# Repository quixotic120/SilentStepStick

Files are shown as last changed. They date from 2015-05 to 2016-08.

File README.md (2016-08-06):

# fork of SilentStepStick
The Silent-Step-Stick is a Stepper Motor Driver Board based on a [Trinamic TMC 2100](http://www.trinamic.com/products/integrated-circuits/stepper-power-driver/tmc2100) or [Trinamic TMC 2130](http://www.trinamic.com/products/integrated-circuits/stepper-power-driver/tmc2130).
The driver boards are hardware compatible with [StepStick](http://reprap.org/wiki/StepStick) and [Pololu A4988](https://www.pololu.com/product/1182).

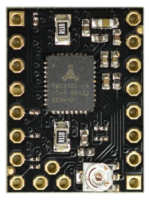
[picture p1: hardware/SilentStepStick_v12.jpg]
SilentStepStick TMC2100 (3.3-5V) (http://www.watterott.com/en/SilentStepStick)

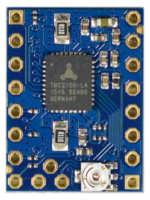
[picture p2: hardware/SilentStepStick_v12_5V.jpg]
SilentStepStick TMC2100 (5V) (http://www.watterott.com/en/SilentStepStick-TMC2100-5V)

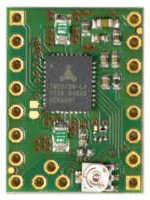
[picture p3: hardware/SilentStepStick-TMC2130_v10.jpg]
SilentStepStick TMC2130 (3.3-5V) (http://www.watterott.com/en/SilentStepStick-TMC2130)

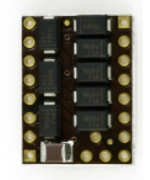
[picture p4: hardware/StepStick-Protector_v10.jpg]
SilentStepStick Protector (http://www.watterott.com/en/SilentStepStick-Protector)


## Shop
* Trinamic **TMC2100** based drivers (CFG pins for configuration)
  * [TMC2100 SilentStepStick (3.3-5V logic voltage)](http://www.watterott.com/en/SilentStepStick)
  * [TMC2100 SilentStepStick (3.3-5V logic voltage) with soldered Pin Headers](http://www.watterott.com/en/SilentStepStick-with-Pins)
  * [TMC2100 SilentStepStick (5V logic voltage)](http://www.watterott.com/en/SilentStepStick-TMC2100-5V)
  * [TMC2100 SilentStepStick (5V logic voltage) with soldered Pin Headers](http://www.watterott.com/en/SilentStepStick-TMC2100-5V-with-Pins)
* Trinamic **TMC2130** based drivers (SPI for configuration)
  * [TMC2130 SilentStepStick (3.3-5V logic voltage)](http://www.watterott.com/en/SilentStepStick-TMC2130)
* Accessories
  * [SilentStepStick Protector (with flyback diodes)](http://www.watterott.com/en/SilentStepStick-Protector)
  * [Suitable Heatsink 10x10mm](http://www.watterott.com/en/Pin-heatsink-square-ICK-S-10-x-10-x-125)
  * [Suitable Heatsink 10x6mm](http://www.watterott.com/en/Heatsink-for-DIL-IC-PLCC-und-SMD-10-x-6-mm)
  * [Suitable Heatsink 8x6mm](http://www.watterott.com/en/Heatsinks-6-3x8mm)

## Features
* Hardware compatible with [StepStick](http://reprap.org/wiki/StepStick) and [Pololu A4988](https://www.pololu.com/product/1182)
* Trinamic TMC21x0 stepper motor driver
* Step/Dir interface with up to 16 microsteps and 256 microsteps interpolation
* Motor current: up to **1.2A RMS** continuously and 2.5A short time peak current per coil
* Motor voltage: **5.5...45V** (3.3...5V logic) or **4.75...45V** (5V logic)
* **microPlyer** - microstep interpolator for increased smoothness of microstepping
* **stealthChop** - for quiet operation and smooth motion
* **spreadCycle** - highly dynamic motor control chopper
* Extra features of **TMC2130**:
  * SPI configuration interface (up to 4MHz)
  * up to 256 native microsteps (without interpolation)
  * **coolStep** - current control for energy savings
  * **stallGuard** - sensorless motor load detection
  * **dcStep** - load dependent speed control

## Hardware
* [Schematics/Layout + Guide](https://github.com/watterott/SilentStepStick/tree/master/hardware)
* [FAQ (Frequently Asked Questions)](https://github.com/watterott/SilentStepStick/blob/master/docu/FAQ.md)
* [Eagle CAD Part](https://github.com/watterott/Eagle-Libs)

## Reviews and Tests

* Review from Thomas Sanladerer:

  SilentStepStick/TMC2100 Review (https://www.youtube.com/watch?v=g6Bxoqr8QlY)

  SilentStepStick/TMC2100 Review Update (https://www.youtube.com/watch?v=mYuZqx8xwTg)

* Review from Peter Recktenwald:

  SilentStepStick/TMC2100 Review (https://www.youtube.com/watch?v=P3ebhi-vZRY)

* Review from Georg Mill:

  [](http://blog.georgmill.de/2015/06/18/schrittmotor-test-5-treiber-im-vergleich/)

* What is Trinamic stallGuard2 and coolStep:

  Trinamic stallGuard2 and coolStep (https://www.youtube.com/watch?v=Prw7wNa20Gk)

* Tests:
  * [Watterott (Stepper Motor)](https://www.youtube.com/watch?v=0l-HlntFYOY)
  * [Aleks (RepRap Prusa i3)](https://www.youtube.com/watch?v=33jQ0P7SMJA)
  * [Anthony (Delta Printer)](https://www.youtube.com/watch?v=CZOV0BdgSiU)
  * [Mario Lukas](https://www.youtube.com/watch?v=mJmg0iRHX8s)
  * Yusuke Sasaki: [TMC2100 steahlChop](https://www.youtube.com/watch?v=wrS7l46YJ_E), [TMC2100 spreadCycle](https://www.youtube.com/watch?v=391TY72wzPQ), [A4988](https://www.youtube.com/watch?v=iw6MRjzS6V4)
  * [MakerSpatz (Ultimaker)](https://www.youtube.com/watch?v=0jPbzB7XtWg)
  * [Aitor Esteve Alvarado (Ninja Prusa i3)](https://www.youtube.com/watch?v=c_TCVirnKJ0)
  * [Artur Wronowski (Delta Printer)](https://www.youtube.com/watch?v=hH2UkAmbfYs)
  * [3D Huynh (Felix 3D)](https://www.youtube.com/watch?v=EglFOpTXPtg)
  * [Easy 3D (Sparkcube)](https://www.youtube.com/watch?v=BxE_F8_Ec8M)
  * [WOLF HSW (linear drive)](https://www.youtube.com/watch?v=wjuAu0WYOPM)
  * Clarence Lee (ATOM Delta Printer): [TMC2100](https://www.youtube.com/watch?v=sBVNqFybUZI), [DRV8825](https://www.youtube.com/watch?v=tNufJnybsxg), [A4982](https://www.youtube.com/watch?v=r1noUt2UoO8)
  * Alex Tien (3DP Delta Printer): [TMC2100](https://www.youtube.com/watch?v=RcqnXXp4tPA), [A4988](https://www.youtube.com/watch?v=F2oB_NOLxHU)
  * swdjojo (Prusa i3): [TMC2100](https://www.youtube.com/watch?v=vBRNifmHaZE), [A4988](https://www.youtube.com/watch?v=TCgErVx93OA)
  * [Doc. Snuggles (Stepper Motor)](https://www.youtube.com/watch?v=gj6f6HSrHc4)
  * [Robert Sertic (Ultimaker)](https://www.youtube.com/watch?v=1wQJZb0gzoE)
  * [Emanuel Kant (Ultimaker)](https://www.youtube.com/watch?v=Y7CG43yf9zA)
  * [ghicione (EggBot)](https://www.youtube.com/watch?v=4FBAAQXnESU)
  * Edward Kuo: [E3D Cyclops Delta Printer](https://www.youtube.com/watch?v=iEYdrMH69oo), [TMC2100 water cooled](https://www.youtube.com/watch?v=vjNM9R0NZG0)
  * [Noah Ahmad Connor (Prusa i3)](https://www.youtube.com/watch?v=mNdl3s8TYmY)
  * [Sterillium (XYZ DaVinci)](https://www.youtube.com/watch?v=k-szP5wuplM)
  * [markg21405 (Delta Printer)](https://www.youtube.com/watch?v=tytL3KeIlLw)
  * [JJiG (MakerFarm Pegasus)](https://www.youtube.com/watch?v=9Rny6n1MCfI)
  * [René Jurack (Skimmy v3)](https://www.youtube.com/watch?v=qpl8v0k1_34)
  * [David Spaulding (A4988 vs. TMC2100)](https://www.youtube.com/watch?v=Z5OQpMSvWvs)
  * [Tarjeik (DRV8825 vs. TMC2100)](https://www.youtube.com/watch?v=oNAHOOolHWw)

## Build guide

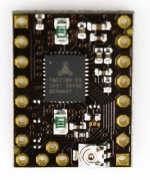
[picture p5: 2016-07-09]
hardware/SilentStepStick_v11.jpg

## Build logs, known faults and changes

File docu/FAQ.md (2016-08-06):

# Frequently Asked Questions

## Is the SilentStepStick 100% compatible with a StepStick or Pololu A4988?
The SilentStepStick is hardware/pin compatible with StepStick and Pololu A4988 drivers.
However the TMC2100 has different and more settings, which can be set via the CFG/MS pins.
The TMC2100 config pins also know three states: low (GND), high (VIO) and open (unconnected).
On the TMC2130 SPI is used for the configuration and so the controller board must have SPI on the CFG pins.

## Where can I find more information on the settings and operation modes?
More information can be found in the [SilentStepStick schematics](https://github.com/watterott/SilentStepStick/tree/master/hardware) and [TMC2100 datasheet](http://www.trinamic.com/products/integrated-circuits/stepper-power-driver/tmc2100) / [TMC2130 datasheet](http://www.trinamic.com/products/integrated-circuits/stepper-power-driver/tmc2130).
For most cases the **1/16 stealthChop** mode (CFG1=open, CFG2=open, CFG3=open) is suitable.
If you have problems like step losses then use the more powerful **1/16 spreadCycle** mode (CFG1=GND, CFG2=open, CFG3=open).

#### Installation Guides for 3D Printers
* [General (English)](http://reprap.org/wiki/TMC2100)
* [General (German)](http://reprap.org/wiki/TMC2100/de)
* [General (Russian)](http://3deshnik.ru/blogs/akdzg/chto-zhe-delat-belami-tmc2100)
* [General (Japanese)](http://3dp0.com/silentstepstick)
* [RAMPS (English)](http://www.instructables.com/id/Install-and-configure-SilentStepStick-in-RAMPS-TMC/)
* [Ultimaker UMO + TMC2100 (English)](https://ultimaker.com/en/community/11571-step-by-step-installation-of-silentstepstick-drivers-on-umo)
* [Ultimaker UMO + TMC2130 (English)](https://ultimaker.com/en/community/20090-step-by-step-installation-of-sss-tmc2130-on-umo)

#### Boards with USB Power Supply and SilentStepSticks with 3.3...5V logic voltage
If you use a control board with USB power supply (like Arduino + RAMPS) then always ensure that ```VM``` is present, when you connect the board via USB.
Otherwise the TMC21x0 is not powered via the internal voltage regulator and a high current can flow into ```VIO``` and this can damage the internal logic.
As safety workaround you can disconnect the 5V signal in the USB cable, so that the board cannot be powered over USB.

#### RAMPS 1.4 and RUMBA Notes
If you remove all jumpers (or open all switches) for MS1+MS2+MS3, then the SilentStepStick TMC2100 driver will be in 1/16 spreadCycle mode (CFG1=GND, CFG2=open, CFG3=open), because there is a pull-down resistor on MS1 on the RAMPS.
But if you have not an original [RAMPS 1.4](http://reprap.org/wiki/RAMPS_1.4) or [RUMBA](http://reprap.org/wiki/RUMBA), then your schematics can be different and you have to check the MS-Pin configurations on you board.

## How to set the stepper motor current?
The best way to set the motor current is by measuring the voltage on the ```Vref``` pin (0...2.5V) and
adjusting the voltage with the potentiometer.
The maximum motor current is 1.77A RMS and is set via the 0.11Ohm sense resistors.

```Irms = (Vref * 1.77A) / 2.5V = Vref * 0.71```

```Vref = (Irms * 2.5V) / 1.77A = Irms * 1.41```

**Example:** A voltage of 1.0V on Vref sets the motor current to 0.71A RMS.

**Note:** On some stepper motor drivers the maximum current (e.g. A4988) is set via Vref and on others the RMS current (e.g. TMC2100).
          ```Imax = 1.41 * Irms```

## What to consider when turning the power supply on or off?
**Power on:**
The motor supply voltage ```VM``` should come up first and then ```VIO```, because the internal logic of the TMC21x0 driver is powered from ```VM``` (SilentStepSticks with 3.3...5V logic voltage).
Only after ```VIO``` is present and stable, the driver inputs (STEP, DIR, EN, CFG1...) can be driven with a high level.

Because ```VM``` is a strong power supply with a high voltage, also ensure that there cannot occur voltage spikes on power up. See [Pololu: Understanding Destructive LC Voltage Spikes](https://www.pololu.com/docs/0J16/all).

**Power off:**
If the motor is running/moving, then it is not allowed to switch off the power supply. Always make sure that the motor stands still on shutting down otherwise the TMC21x0 driver can get damaged.
An **emergency stop** can be realized, when the ```EN/CFG6``` pin is set to ```VIO```. This will switch off all power drivers and will put the motor into freewheeling.
See also: [SilentStepStick Protector with flyback diodes](https://github.com/watterott/SilentStepStick#shop)

## The motor makes noise in spreadCycle mode when it is not moving?
A motor supply voltage of 12V is in most cases to low and in general the sound gets quieter if the motor supply voltage is above 18V.

## How to control the TMC21x0 stepper motor driver?
The SilentStepStick has a normal step+direction interface.
You set the direction with the ```DIR``` pin and on every pulse on the ```STEP``` pin the motor will move one step.
Here you can find an [Arduino example](https://github.com/watterott/SilentStepStick/tree/master/software) and [Arduino library](http://www.airspayce.com/mikem/arduino/AccelStepper/) (interface=DRIVER).

## Is it possible to connect the CFG pins from different SilentStepSticks?
It is possible to connect the ```CFG``` pins from two or more driver boards.
However then the pin state can only be ```GND``` (low) or ```VIO``` (high). The open state (unconnected) is not possible in this configuration.

## Why is the TMC2100 chip on the bottom PCB side?
The TMC2100/TMC2130 chip has a thermal pad on the bottom which is soldered to the PCB.
So the thermal resistance via the chip bottom is better than via the top.
That is why the chip is on the bottom PCB side.
A heat sink can be placed directly on the PCB.
Further infos [here](https://www.youtube.com/watch?time_continue=145&v=mYuZqx8xwTg).

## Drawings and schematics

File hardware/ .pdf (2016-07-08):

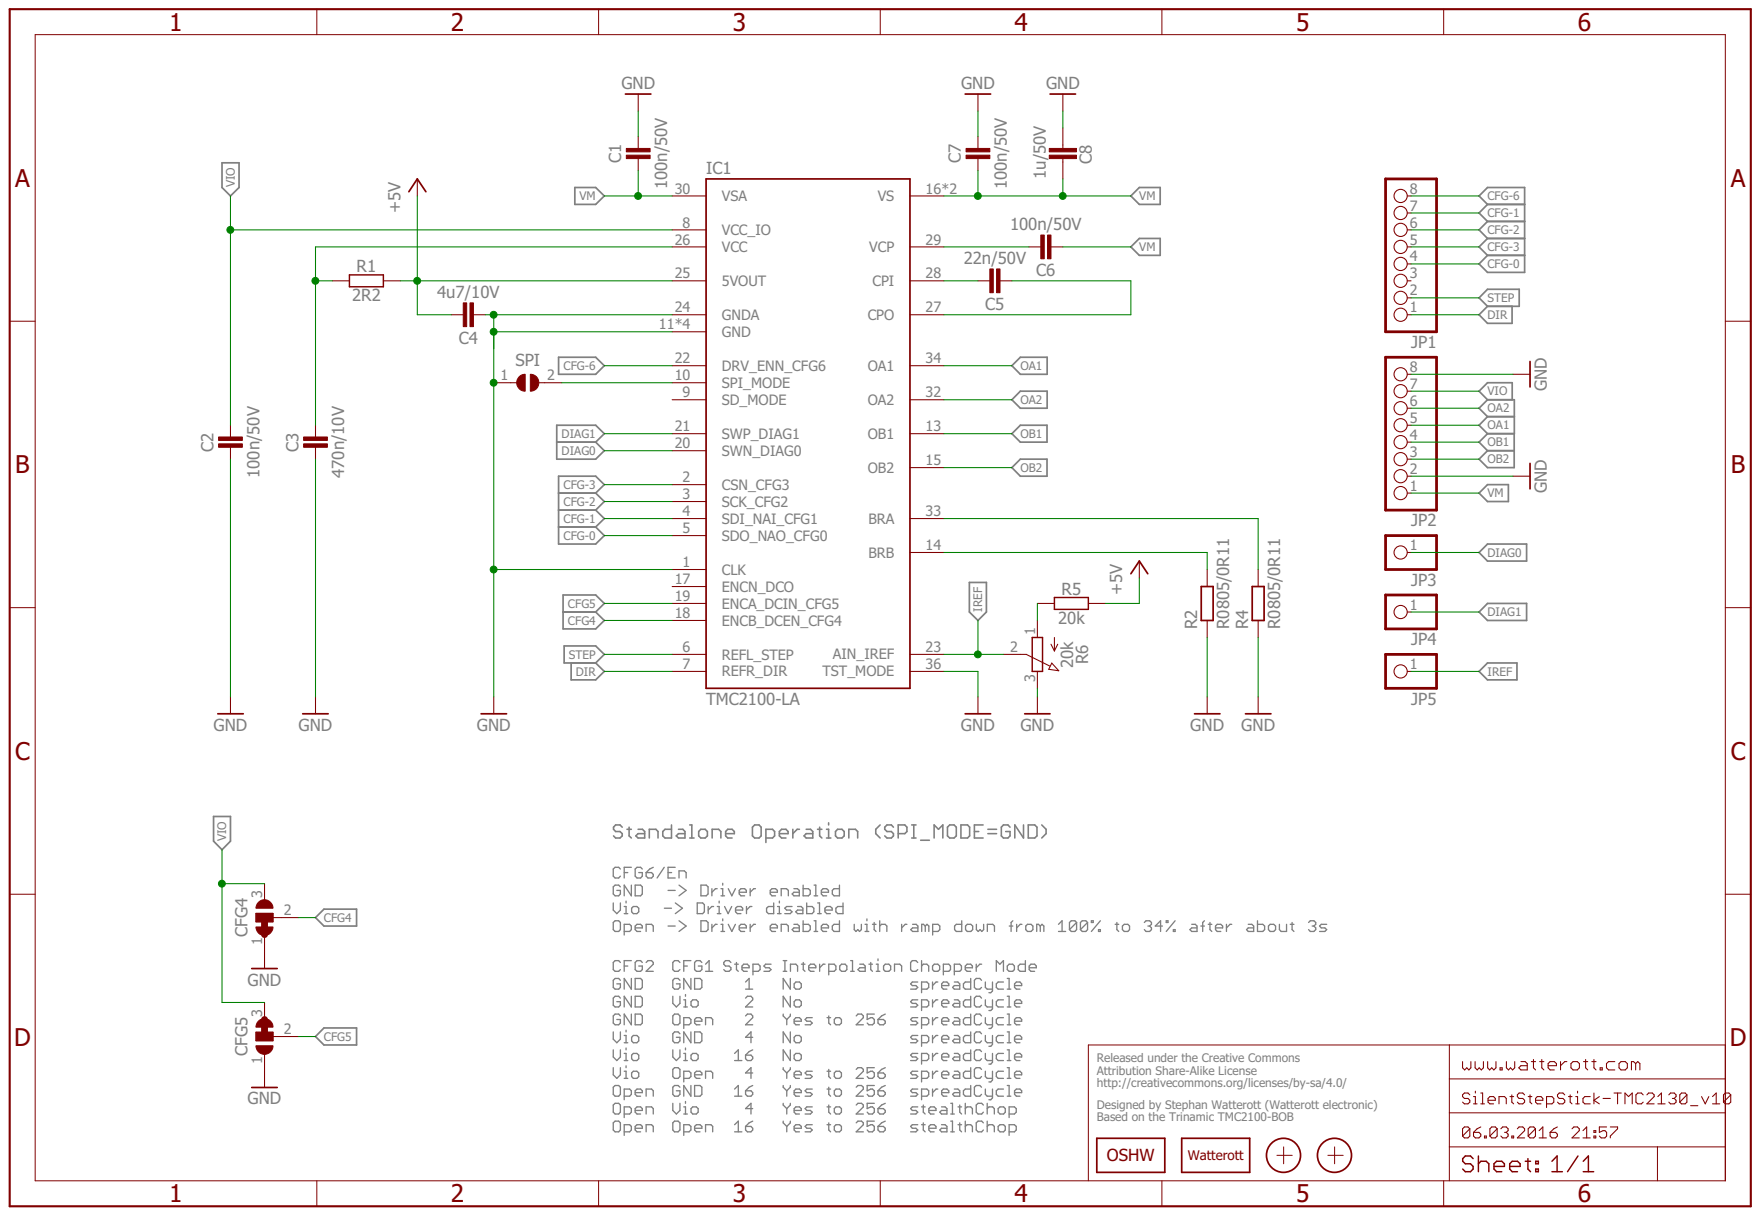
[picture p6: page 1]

VCC 26

R1 | 5VOUT 25

GNDA 24

Released under the Creative Commons
Attribution Share-Alike License
http://creativecommons.org/licenses/by-sa/4.0/

Designed by Stephan Watterott (Watterott electronic)
Based on the Trinamic TMC2100-BOB

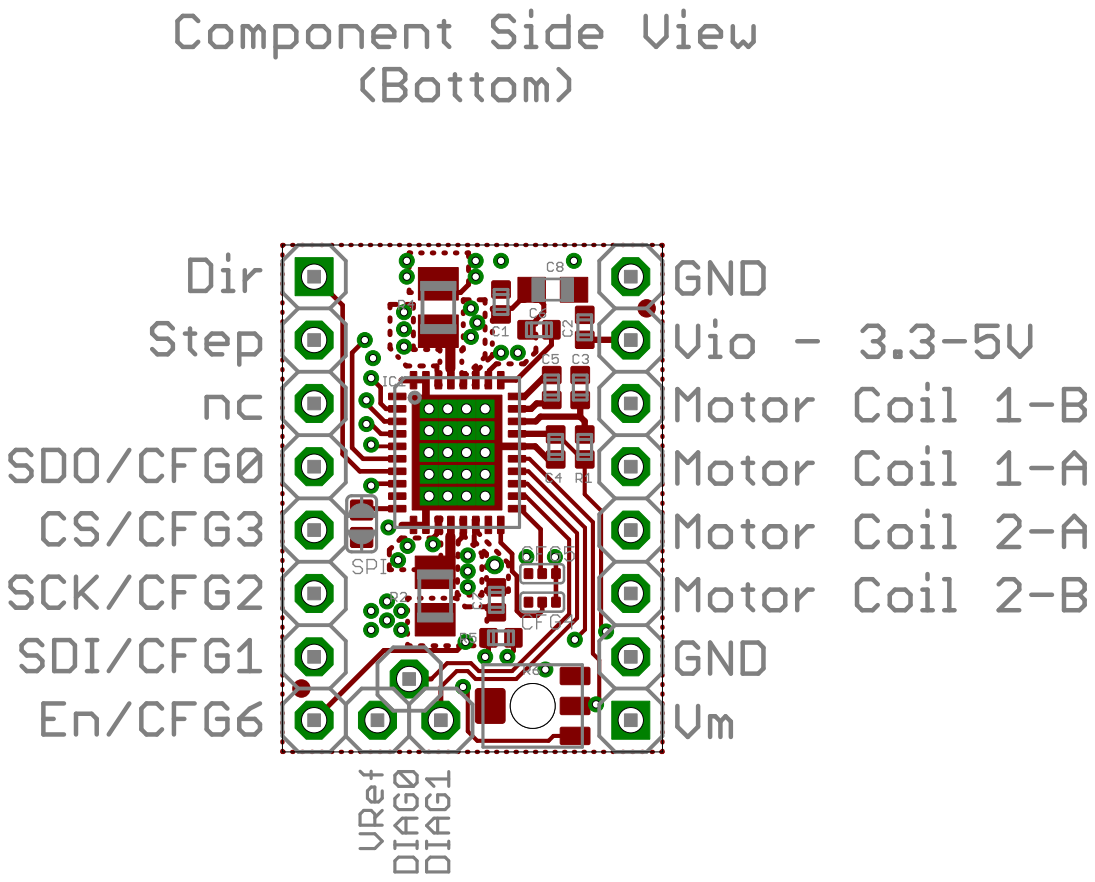
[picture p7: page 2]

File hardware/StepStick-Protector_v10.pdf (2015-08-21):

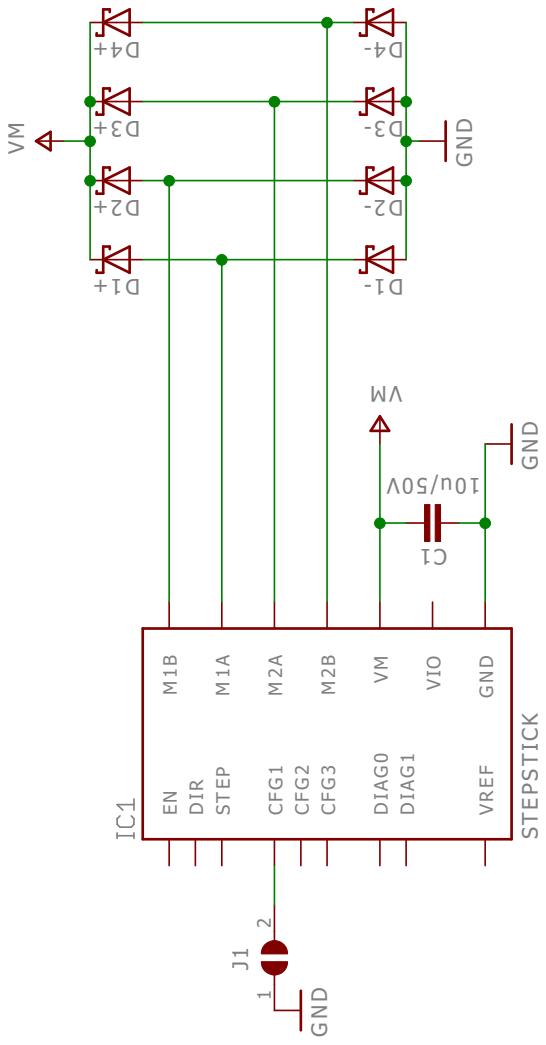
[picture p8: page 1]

GND VM MV GND V05/ u01 GND Released under the Creative Commons Attribution Share-Alike License http://creativecommons.org/licenses/by-sa/4.0/ Designed by Andreas Watterott (Watterott electronic) STEPSTICK DIR STEP CFG1 CFG2 CFG3 DIAG0 EN VM VIO GND M1A DIAG1 M2A M1B M2B VREF +1 D +2 D +3 D +4 D - 1 D - 2 D - 3 D - 4 D 1 C J1 2 1 ABCD 1 2 3 4 5 6 ABCD 1 2 3 4 5 6 OSHW LOGO Logo

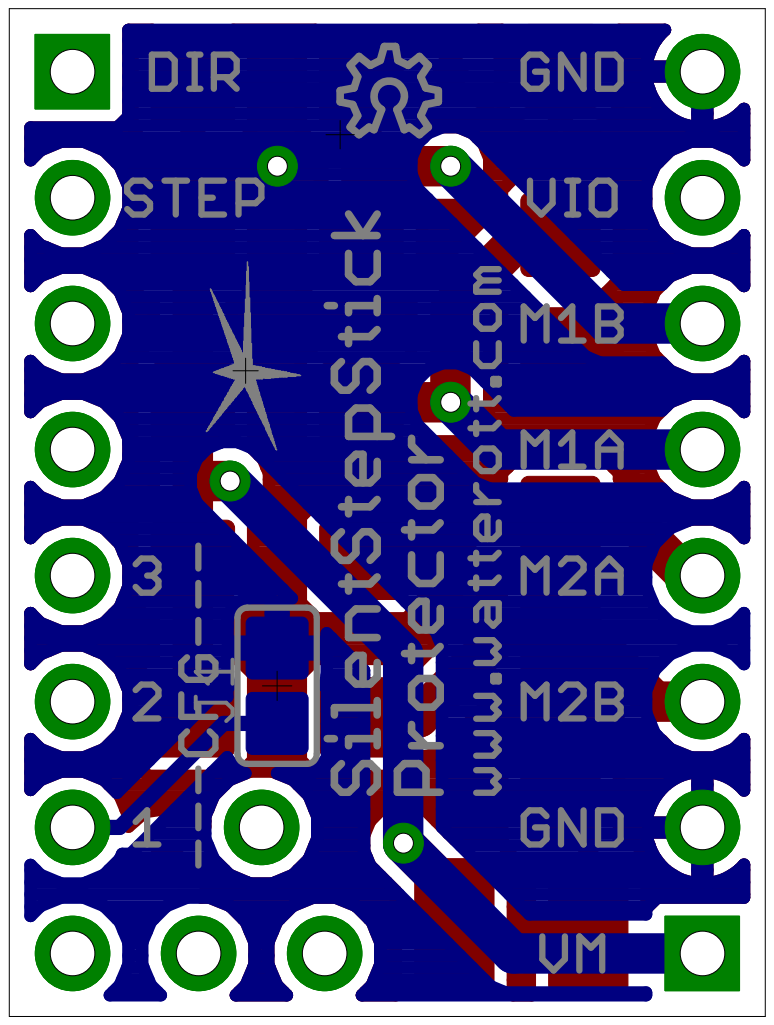
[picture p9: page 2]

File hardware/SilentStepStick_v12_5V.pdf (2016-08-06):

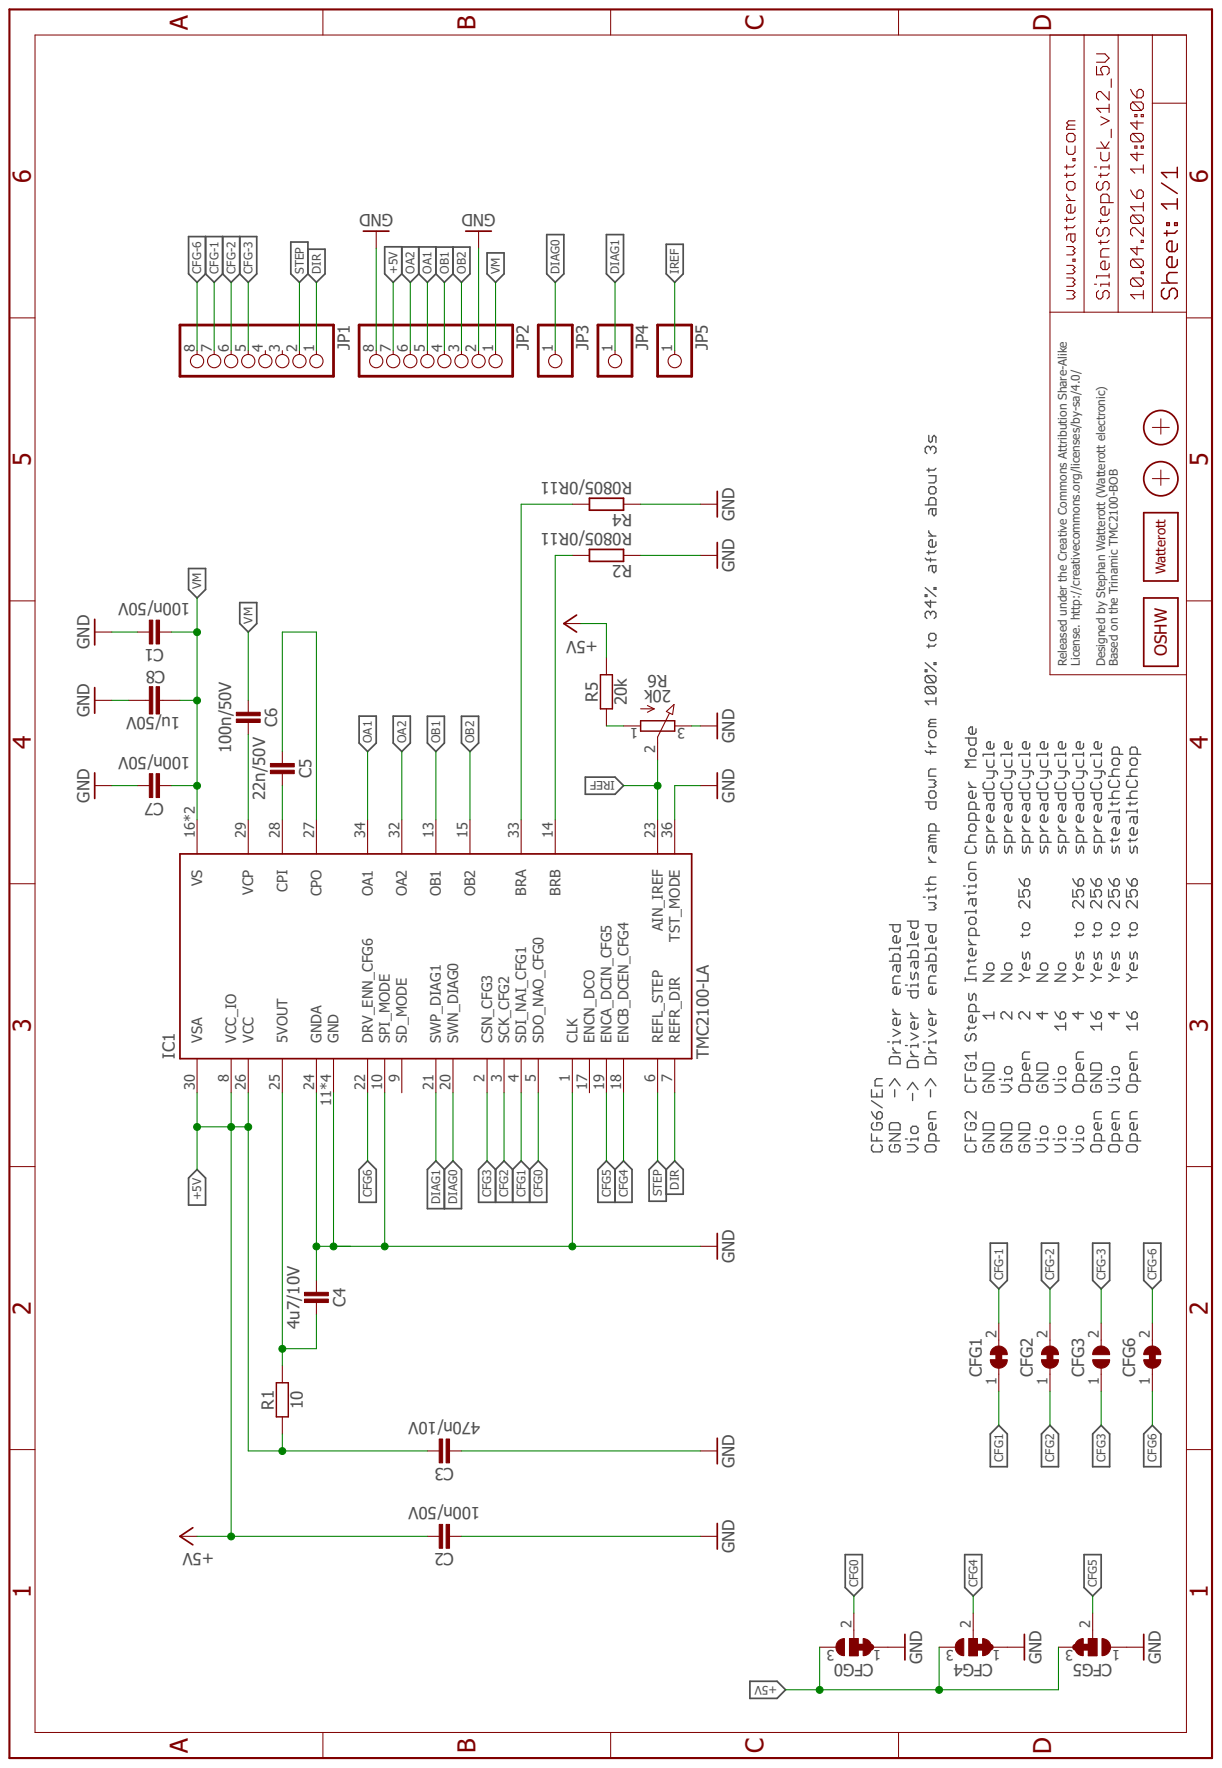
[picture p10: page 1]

Released under the Creative Commons At ribution Share-Alike

License. ht p://creativecommons.org/licenses/by-sa/4.0/ Designed by Stephan Wat erot (Wat erot electronic) Based on the Trinamic TMC2100-BOB

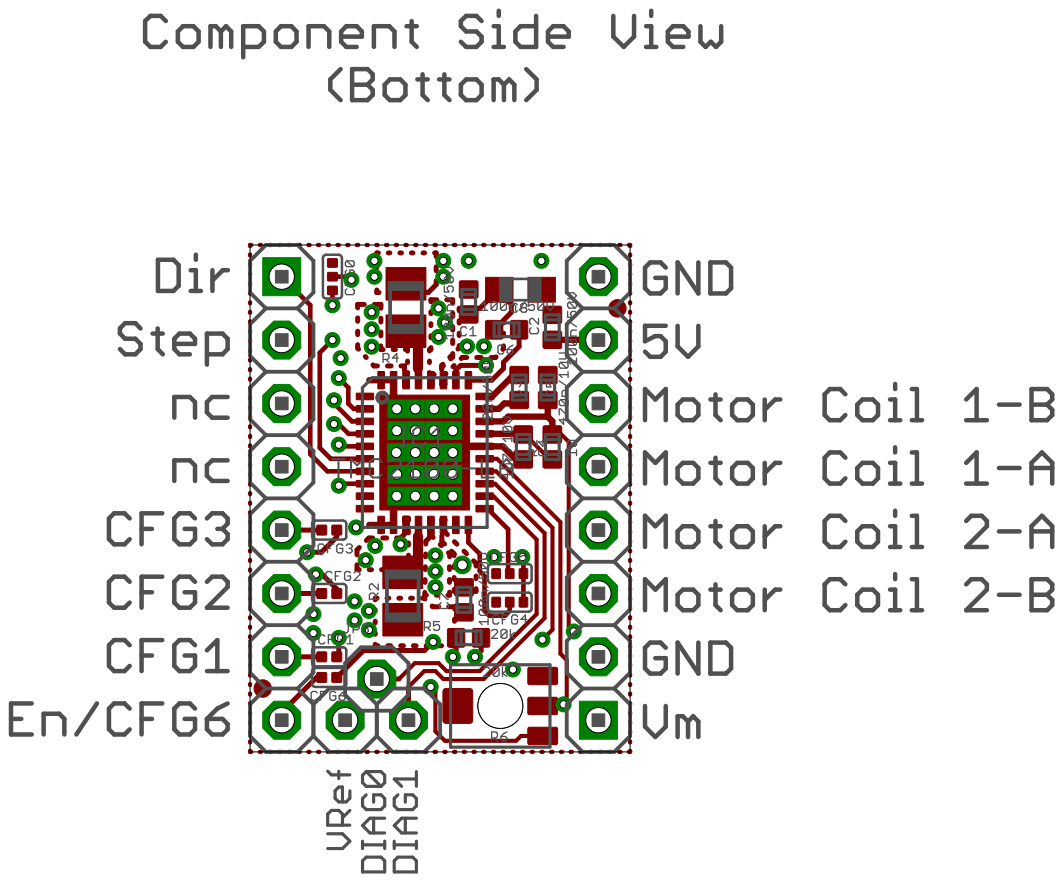
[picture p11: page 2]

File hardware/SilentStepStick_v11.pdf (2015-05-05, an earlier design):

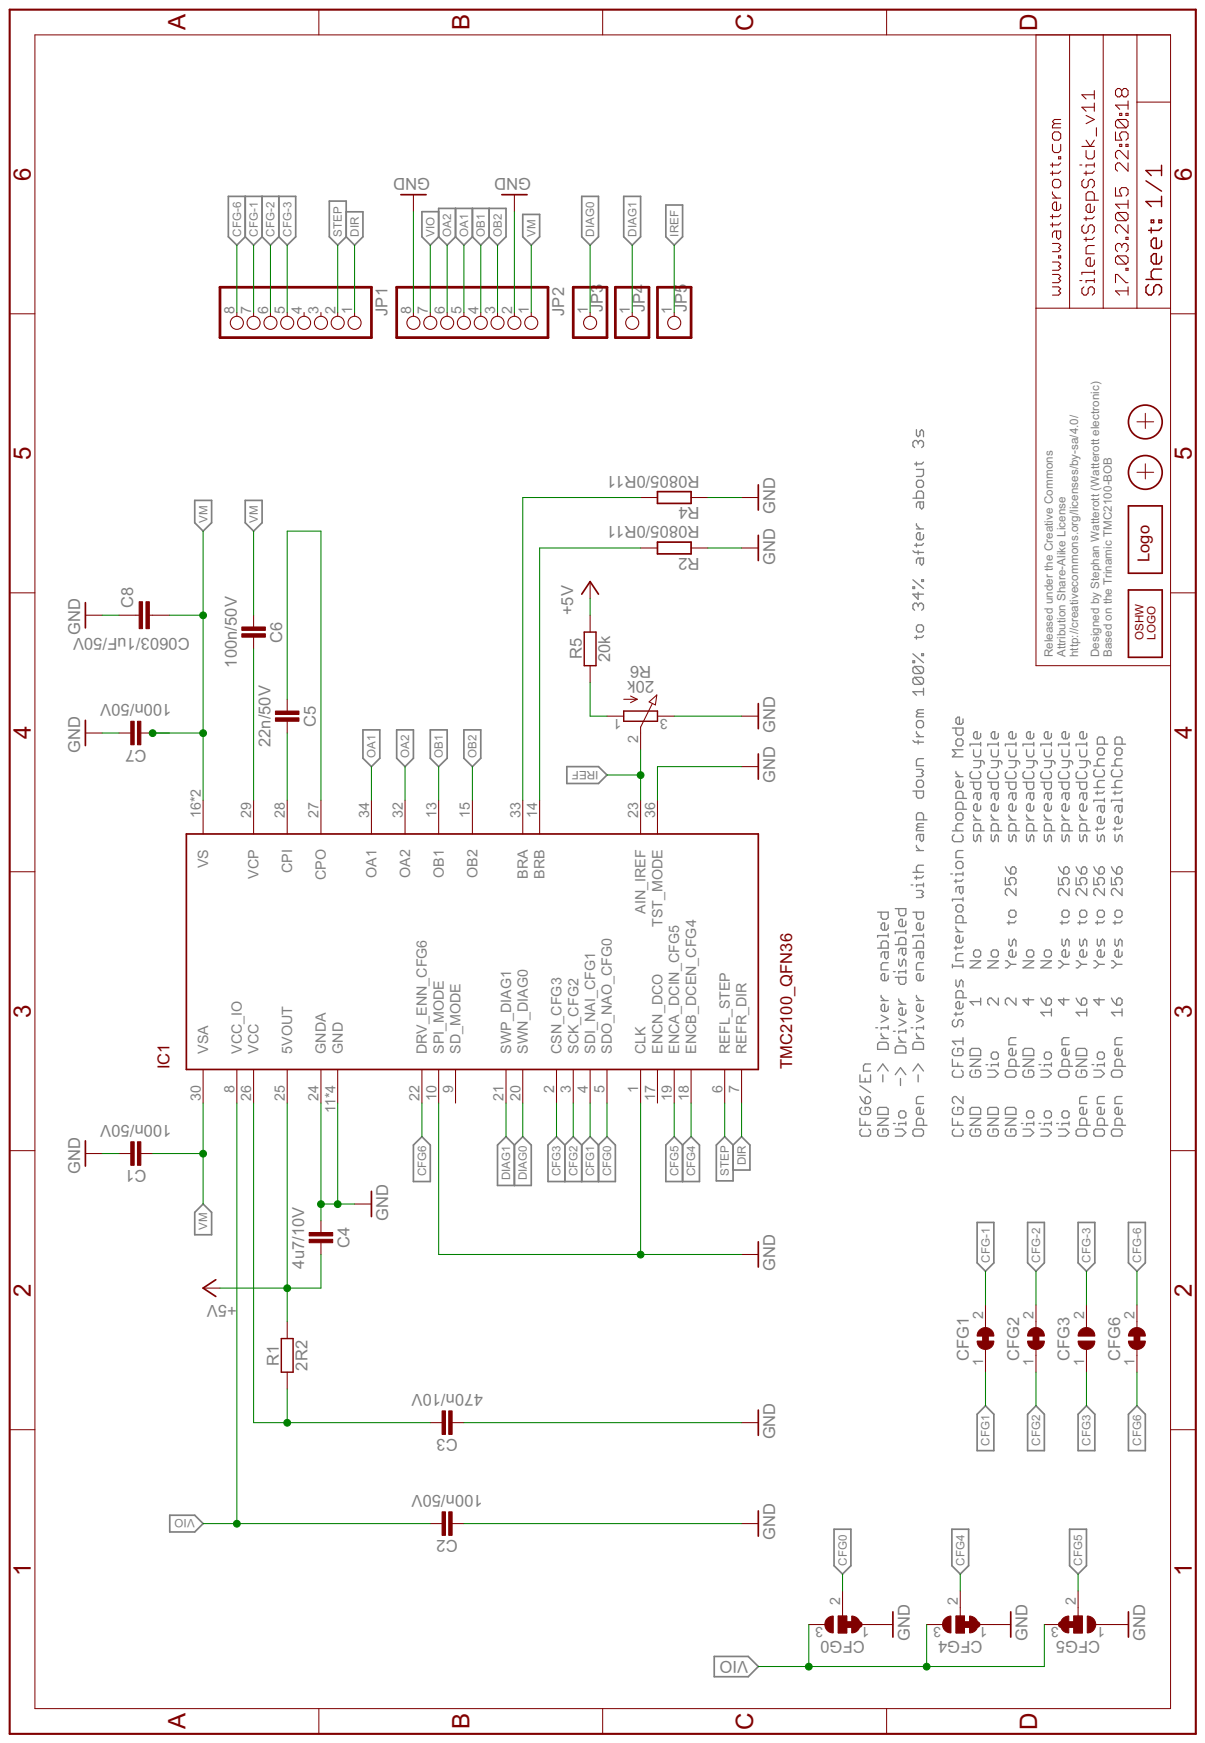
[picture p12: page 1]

Designed by Stephan Watterott (Watterott electronic)

http://creativecommons.org/licenses/by-sa/4.0/

Released under the Creative Commons

Based on the Trinamic TMC2100-BOB

GND GND

Attribution Share-Alike License

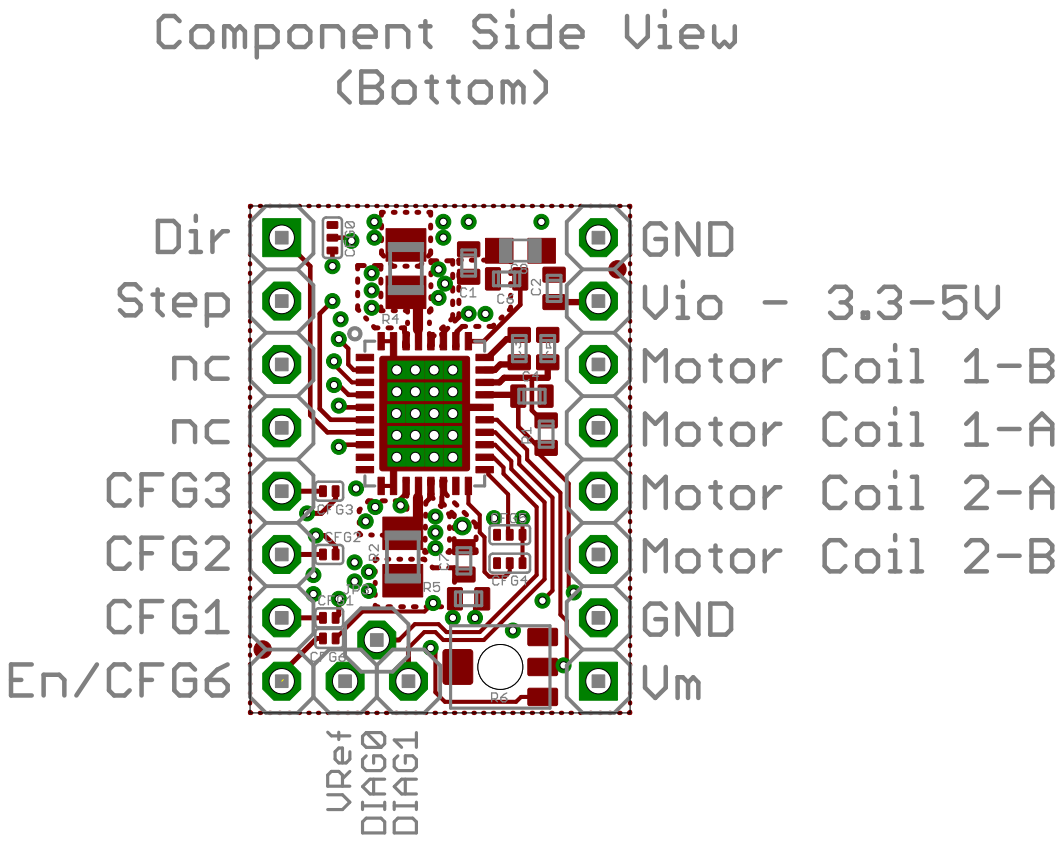
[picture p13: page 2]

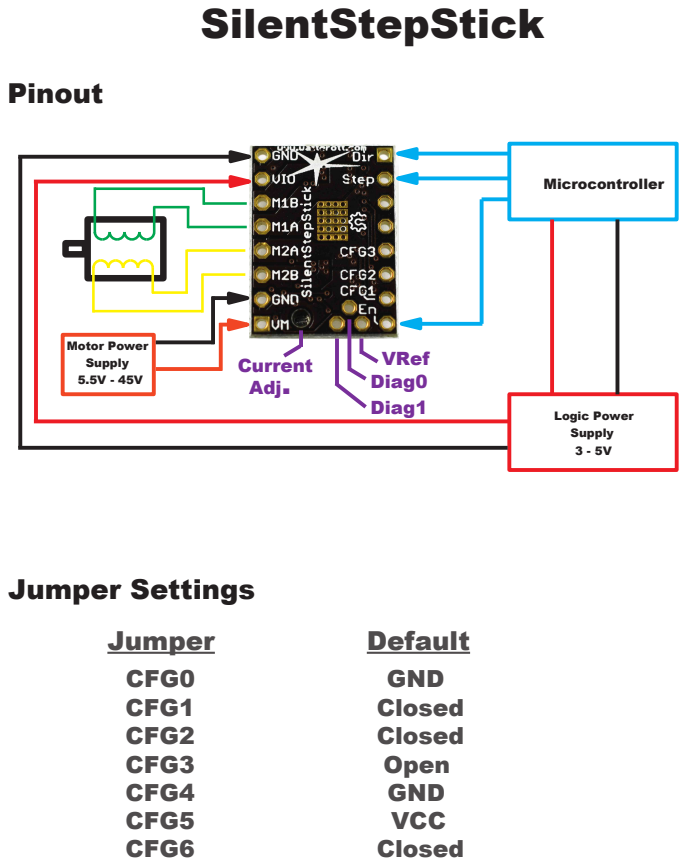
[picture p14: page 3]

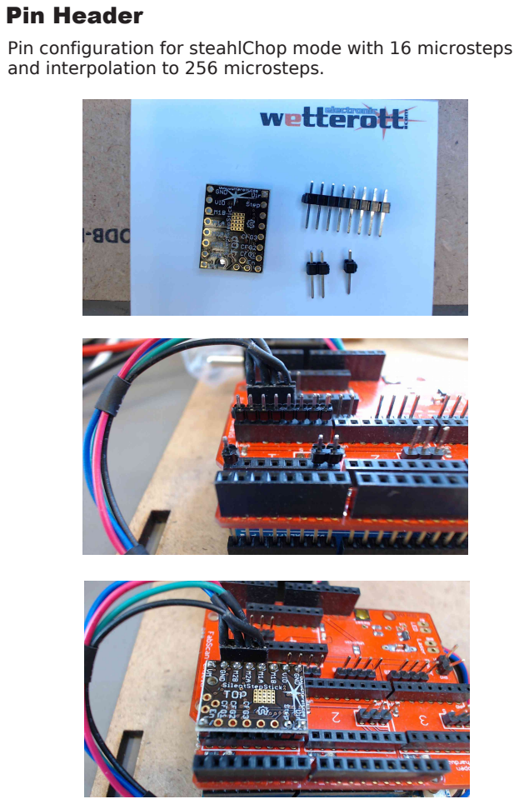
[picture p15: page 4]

Pin configuration for steahlChop mode with 16 microsteps
and interpolation to 256 microsteps.

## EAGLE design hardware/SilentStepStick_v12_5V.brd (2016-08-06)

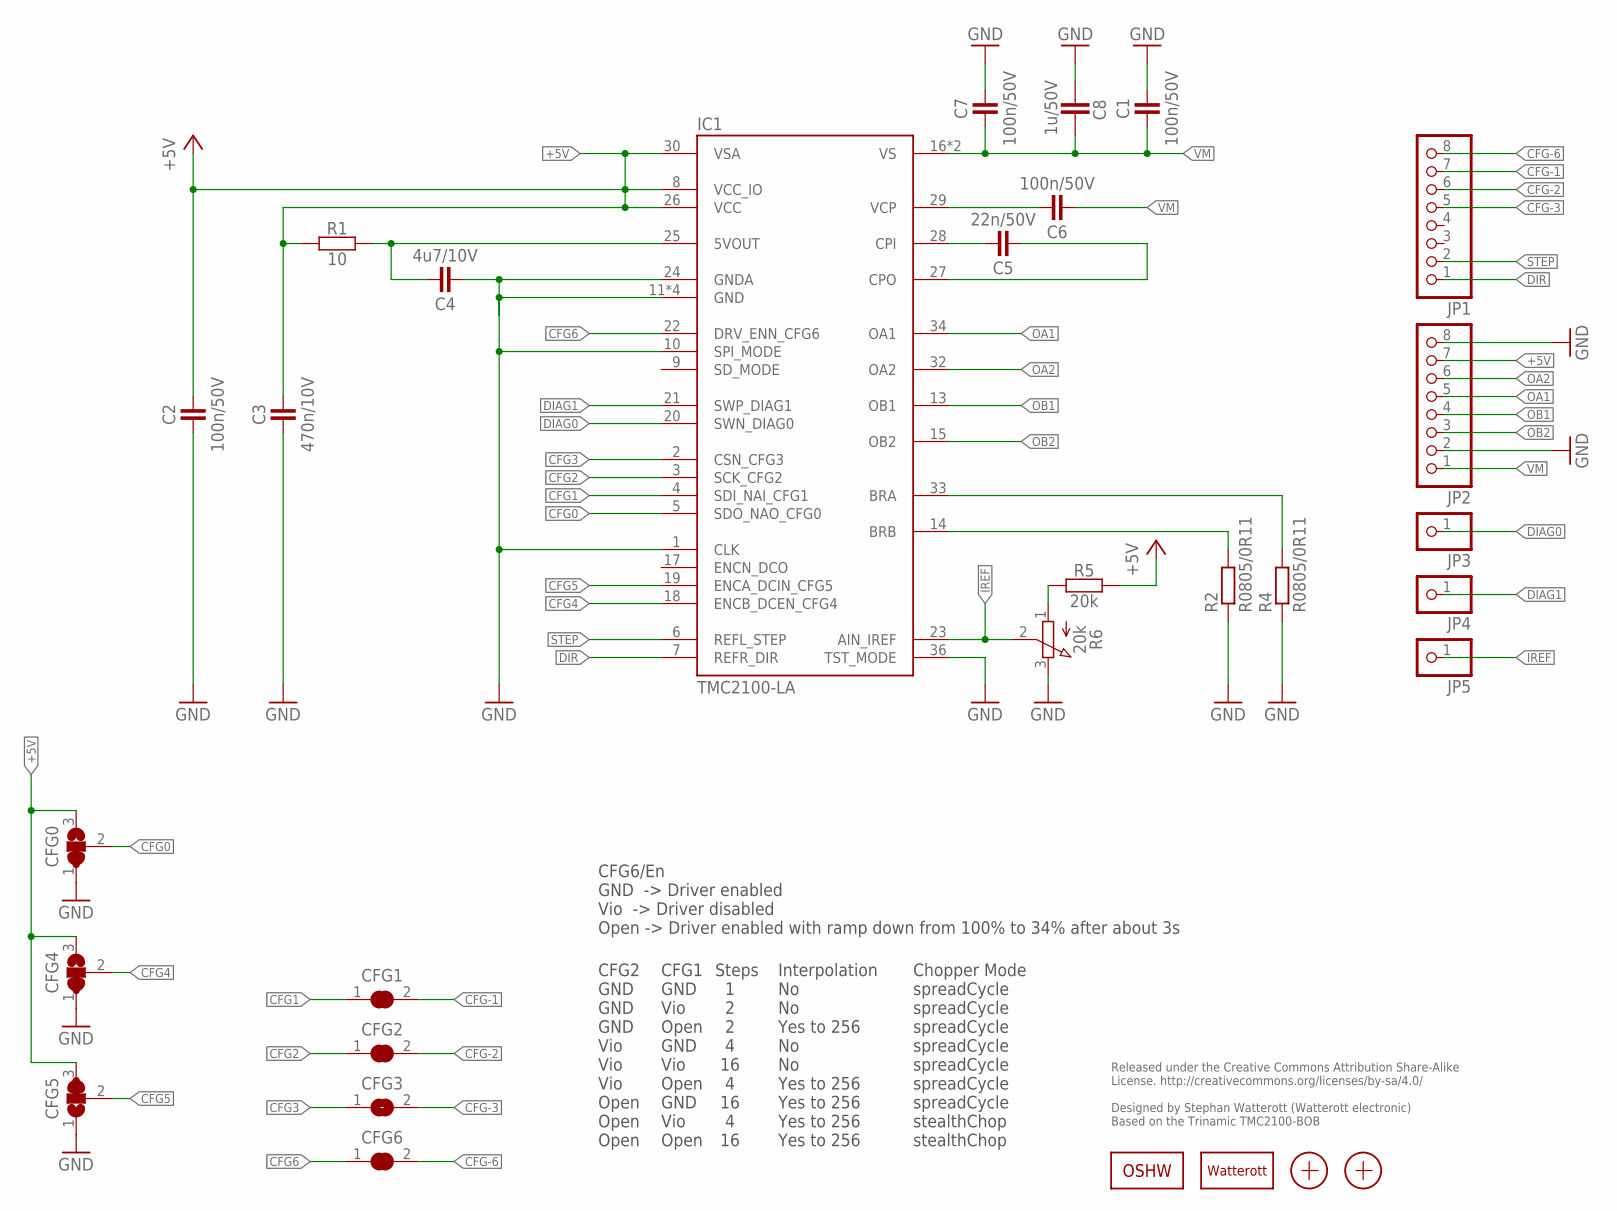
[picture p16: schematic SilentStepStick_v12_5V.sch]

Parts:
C1, C2, C6, C7: 100n/50V; C0402
C3: 470n/10V; C0402
C4: 4u7/10V; C0402
C5: 22n/50V; C0402
C8: 1u/50V; C0603
CFG0, CFG4, CFG5: JUMPER3-0201
CFG1, CFG2, CFG3, CFG6: JUMPER2-0201
IC1: TMC2100-LA; QFN36-PAD
JP1, JP2: PINHD-1X08_2.54-S; 1X08-S
JP3, JP4, JP5: PINHD-1X1; 1X01
LOGO1: OSHW_LOGOX0070; OSHW_6X70
LOGO2: LOGO-S_PLACE_M; SPARK_TPLACE_M
R1: 10; C0402
R2, R4: R0805/0R11; M0805
R5: 20k; C0402
R6: 20k; POT_EVM3R
X1, X2: PASSER-07; PASSER_07MM

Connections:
5VOUT: C4.2, IC1.25 (5VOUT), R1.2
+5V: C2.2, C3.2, CFG0.3, CFG4.3, CFG5.3, IC1.8 (VCC_IO), IC1.26 (VCC), IC1.30 (VSA), JP2.7, R1.1, R5.2
BRA: IC1.33 (BRA), R4.2
BRB: IC1.14 (BRB), R2.2
CFG0: CFG0.2, IC1.5 (SDO_NAO_CFG0)
CFG1: CFG1.1, IC1.4 (SDI_NAI_CFG1)
CFG2: CFG2.1, IC1.3 (SCK_CFG2)
CFG3: CFG3.1, IC1.2 (CSN_CFG3)
CFG4: CFG4.2, IC1.18 (ENCB_DCEN_CFG4)
CFG5: CFG5.2, IC1.19 (ENCA_DCIN_CFG5)
CFG6: CFG6.1, IC1.22 (DRV_ENN_CFG6)
CFG-1: CFG1.2, JP1.7
CFG-2: CFG2.2, JP1.6
CFG-3: CFG3.2, JP1.5
CFG-6: CFG6.2, JP1.8
CPI: C5.2, IC1.28 (CPI)
CPO: C5.1, IC1.27 (CPO)
DIAG0: IC1.20 (SWN_DIAG0), JP3.1
DIAG1: IC1.21 (SWP_DIAG1), JP4.1
DIR: IC1.7 (REFR_DIR), JP1.1
GND: C1.2, C2.1, C3.1, C4.1, C7.2, C8.2, CFG0.1, CFG4.1, CFG5.1, IC1.1 (CLK), IC1.10 (SPI_MODE), IC1.11 (GND), IC1.12 (GND), IC1.24 (GNDA), IC1.35 (GND), IC1.36 (TST_MODE), IC1.TP (GND), JP2.2, JP2.8, R2.1, R4.1, R6.3 (E)
IREF: IC1.23 (AIN_IREF), JP5.1, R6.2 (S)
OA1: IC1.34 (OA1), JP2.5
OA2: IC1.32 (OA2), JP2.6
OB1: IC1.13 (OB1), JP2.4
OB2: IC1.15 (OB2), JP2.3
STEP: IC1.6 (REFL_STEP), JP1.2
VCP: C6.2, IC1.29 (VCP)
VM: C1.1, C6.1, C7.1, C8.1, IC1.16 (VS), IC1.31 (VS), JP2.1
VREF1: R5.1, R6.1 (A)

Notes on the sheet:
Released under the Creative Commons Attribution Share-Alike License. http://creativecommons.org/licenses/by-sa/4.0/ Designed by Stephan Watterott (Watterott electronic) Based on the Trinamic TMC2100-BOB
CFG6/En GND -> Driver enabled Vio -> Driver disabled Open -> Driver enabled with ramp down from 100% to 34% after about 3s
CFG2 GND GND GND Vio Vio Vio Open Open Open
CFG1 GND Vio Open GND Vio Open GND Vio Open
Steps 1 2 2 4 16 4 16 4 16
Interpolation No No Yes to 256 No No Yes to 256 Yes to 256 Yes to 256 Yes to 256
Chopper Mode spreadCycle spreadCycle spreadCycle spreadCycle spreadCycle spreadCycle spreadCycle stealthChop stealthChop

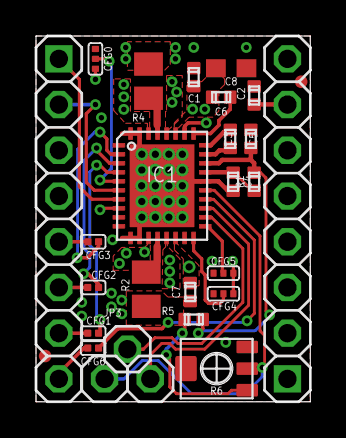
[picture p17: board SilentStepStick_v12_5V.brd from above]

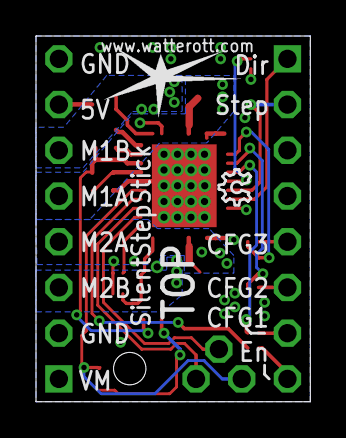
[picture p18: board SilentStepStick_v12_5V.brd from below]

Board: 4 copper layers, 15.2 x 20.3 mm, 30 parts (2 on the bottom side), 30 nets.

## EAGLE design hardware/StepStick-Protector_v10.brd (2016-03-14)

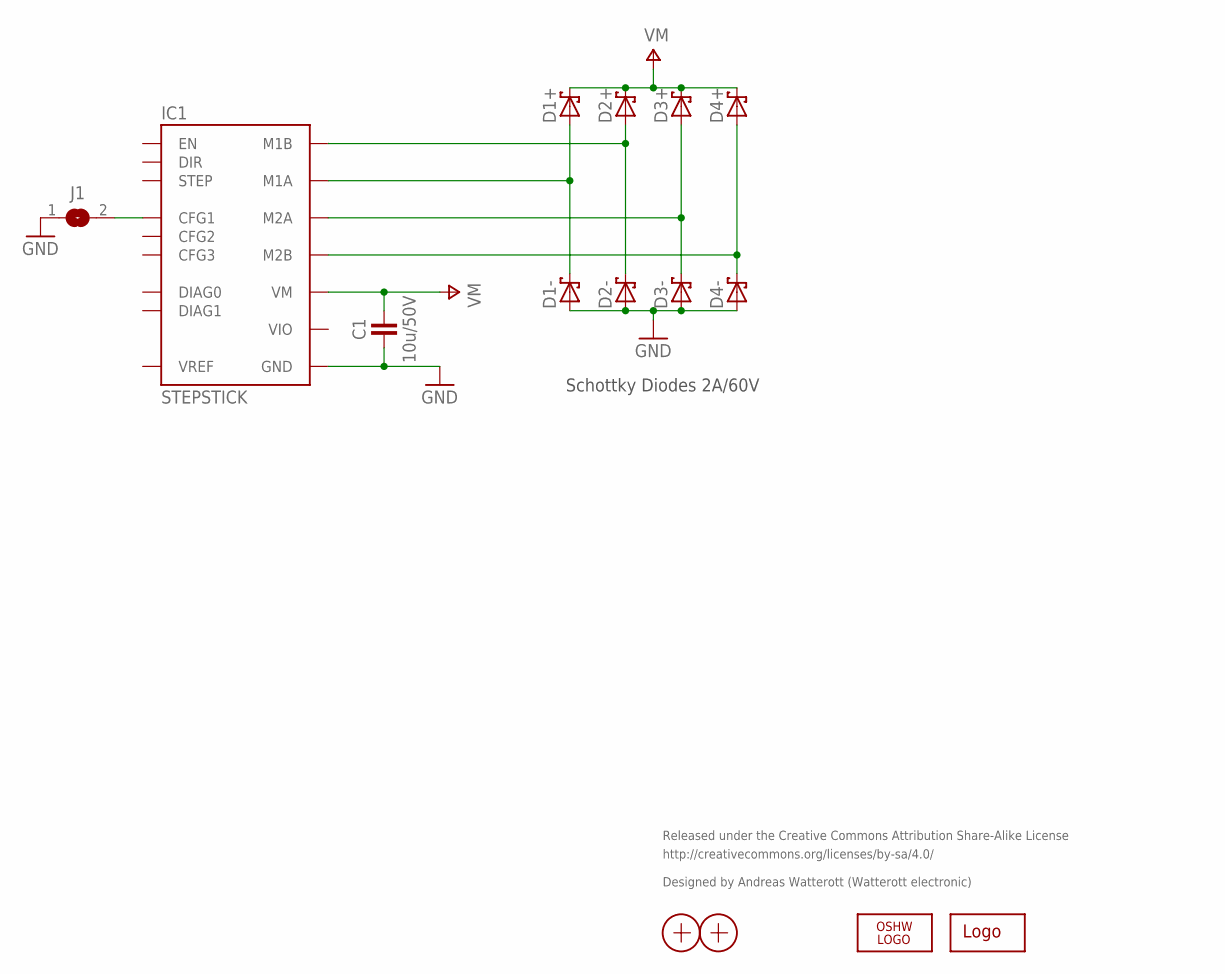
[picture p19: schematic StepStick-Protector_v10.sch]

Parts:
C1: 10u/50V; C1210
D1+, D1-, D2+, D2-, D3+, D3-, D4+, D4-: D_SCHOTTKY-SS14; SMA_DO214AC
IC1: STEPSTICK
J1: JUMPER2-0603-NC; JUMPER2-0603_NC
LOGO1: OSHW_LOGOX0070; OSHW_6X70
LOGO2: LOGO-S_PLACE_S; SPARK_TPLACE_S
X1, X2: PASSER

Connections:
GND: C1.1, D1-.A, D2-.A, D3-.A, D4-.A, IC1.GND@1 (GND), IC1.GND@2 (GND), J1.1
M1A: D1+.A, D1-.C, IC1.M1A
M1B: D2+.A, D2-.C, IC1.M1B
M2A: D3+.A, D3-.C, IC1.M2A
M2B: D4+.A, D4-.C, IC1.M2B
unnamed: IC1.CFG1, J1.2
VIO: IC1.VIO
VM: C1.2, D1+.C, D2+.C, D3+.C, D4+.C, IC1.VM

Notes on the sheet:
Released under the Creative Commons Attribution Share-Alike License
http://creativecommons.org/licenses/by-sa/4.0/
Designed by Andreas Watterott (Watterott electronic)
Schottky Diodes 2A/60V

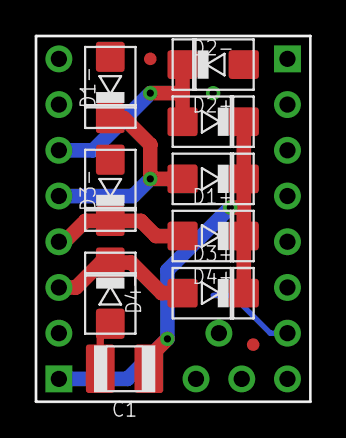
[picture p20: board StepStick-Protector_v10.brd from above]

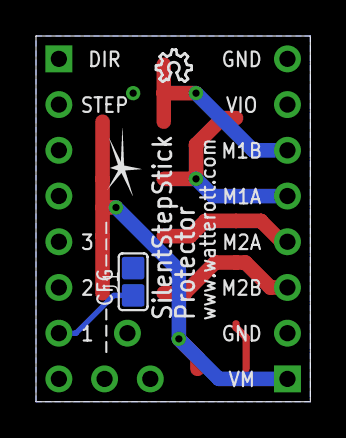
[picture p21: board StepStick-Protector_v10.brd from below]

Board: 2 copper layers, 15.2 x 20.3 mm, 15 parts (3 on the bottom side), 7 nets.

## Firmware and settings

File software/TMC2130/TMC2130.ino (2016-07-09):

/*
  Trinamic TMC2130 Example
*/

#include "SPI.h"

// Note: You also have to connect GND, 5V and VM.
//       A connection diagram can be found in the schematics.
#define EN_PIN    7 //enable (CFG6)
#define DIR_PIN   8 //direction
#define STEP_PIN  9 //step

#define CS_PIN   10 //chip select
#define MOSI_PIN 11 //SDI/MOSI (ICSP: 4, Uno: 11, Mega: 51)
#define MISO_PIN 12 //SDO/MISO (ICSP: 1, Uno: 12, Mega: 50)
#define SCK_PIN  13 //CLK/SCK  (ICSP: 3, Uno: 13, Mega: 52)

//TMC2130 registers
#define WRITE          0x80 //write flag
#define REG_GCONF      0x00
#define REG_GSTAT      0x01
#define REG_IHOLD_IRUN 0x10
#define REG_CHOPCONF   0x6C
#define REG_COOLCONF   0x6D
#define REG_DCCTRL     0x6E
#define REG_DRVSTATUS  0x6F

uint8_t tmc_write(uint8_t cmd, uint32_t data)
{
  uint8_t s;

  digitalWrite(CS_PIN, LOW);

  s = SPI.transfer(cmd);
  SPI.transfer((data>>24UL)&0xFF)&0xFF;
  SPI.transfer((data>>16UL)&0xFF)&0xFF;
  SPI.transfer((data>> 8UL)&0xFF)&0xFF;
  SPI.transfer((data>> 0UL)&0xFF)&0xFF;

  digitalWrite(CS_PIN, HIGH);

  return s;
}

uint8_t tmc_read(uint8_t cmd, uint32_t *data)
{
  uint8_t s;

  tmc_write(cmd, 0UL); //set read address

  digitalWrite(CS_PIN, LOW);

  s = SPI.transfer(cmd);
  *data  = SPI.transfer(0x00)&0xFF;
  *data <<=8;
  *data |= SPI.transfer(0x00)&0xFF;
  *data <<=8;
  *data |= SPI.transfer(0x00)&0xFF;
  *data <<=8;
  *data |= SPI.transfer(0x00)&0xFF;

  digitalWrite(CS_PIN, HIGH);

  return s;
}

void setup()
{
  //set pins
  pinMode(EN_PIN, OUTPUT);
  digitalWrite(EN_PIN, HIGH); //deactivate driver (LOW active)
  pinMode(DIR_PIN, OUTPUT);
  digitalWrite(DIR_PIN, LOW); //LOW or HIGH
  pinMode(STEP_PIN, OUTPUT);
  digitalWrite(STEP_PIN, LOW);

  pinMode(CS_PIN, OUTPUT);
  digitalWrite(CS_PIN, HIGH);
  pinMode(MOSI_PIN, OUTPUT);
  digitalWrite(MOSI_PIN, LOW);
  pinMode(MISO_PIN, INPUT);
  digitalWrite(MISO_PIN, HIGH);
  pinMode(SCK_PIN, OUTPUT);
  digitalWrite(SCK_PIN, LOW);

  //init serial port
  Serial.begin(9600); //init serial port and set baudrate
  while(!Serial); //wait for serial port to connect (needed for Leonardo only)
  Serial.println("\nStart...");

  //init SPI
  SPI.setDataMode(SPI_MODE3);
  SPI.setBitOrder(MSBFIRST);
  SPI.setClockDivider(SPI_CLOCK_DIV128);
  SPI.begin();

  //set TMC2130 config
  tmc_write(WRITE|REG_GCONF,      0x00000001UL); //voltage on AIN is current reference
  tmc_write(WRITE|REG_IHOLD_IRUN, 0x00001010UL); //IHOLD=0x10, IRUN=0x10
  tmc_write(WRITE|REG_CHOPCONF,   0x00008008UL); //native 256 microsteps, MRES=0, TBL=1=24, TOFF=8

  //TMC2130 outputs on (LOW active)
  digitalWrite(EN_PIN, LOW);
}

void loop()
{
  static uint32_t last_time=0;
  uint32_t ms = millis();
  uint32_t data;
  uint8_t s;
    
  if((ms-last_time) > 1000) //run every 1s
  {
    last_time = ms;

    //show REG_GSTAT
    s = tmc_read(REG_GSTAT, &data);
    Serial.print("GSTAT:     0x0");
    Serial.print(data, HEX);
    Serial.print("\t - ");
    Serial.print("Status: 0x");
    Serial.print(s, HEX);
    if(s & 0x01) Serial.print(" reset");
    if(s & 0x02) Serial.print(" error");
    if(s & 0x04) Serial.print(" sg2");
    if(s & 0x08) Serial.print(" standstill");
    Serial.println(" ");

    //show REG_DRVSTATUS
    s = tmc_read(REG_DRVSTATUS, &data);
    Serial.print("DRVSTATUS: 0x");
    Serial.print(data, HEX);
    Serial.print("\t - ");
    Serial.print("Status: 0x");
    Serial.print(s, HEX);
    if(s & 0x01) Serial.print(" reset");
    if(s & 0x02) Serial.print(" error");
    if(s & 0x04) Serial.print(" sg2");
    if(s & 0x08) Serial.print(" standstill");
    Serial.println(" ");
  }

  //make steps
  digitalWrite(STEP_PIN, HIGH);
  delayMicroseconds(10);
  digitalWrite(STEP_PIN, LOW);
  delayMicroseconds(10);
}

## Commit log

2015-01-20 added layout and schematics
    [SilentStepStick_v10.brd, SilentStepStick_v10.sch]
2015-01-21 updated layout and schematics
    [SilentStepStick_v10.brd, SilentStepStick_v10.sch]
2015-01-28 updated schematics
    [SilentStepStick_v10.brd, SilentStepStick_v10.sch]
2015-08-21 changed path structure
    [SilentStepStick_v10.brd, SilentStepStick_v10.sch, SilentStepStick_v11.brd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]
2016-03-06 added TMC2130 layout and schematics
    [SilentStepStick-TMC2130_v10.brd, SilentStepStick-TMC2130_v10.sch]
2016-07-19 added 5V TMC2100 SilentStepStick
    [SilentStepStick_v12_5V.brd, SilentStepStick_v12_5V.sch]
